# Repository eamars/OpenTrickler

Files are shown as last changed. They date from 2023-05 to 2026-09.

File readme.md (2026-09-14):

# Open Trickler - The Open Source Powder Trickler System

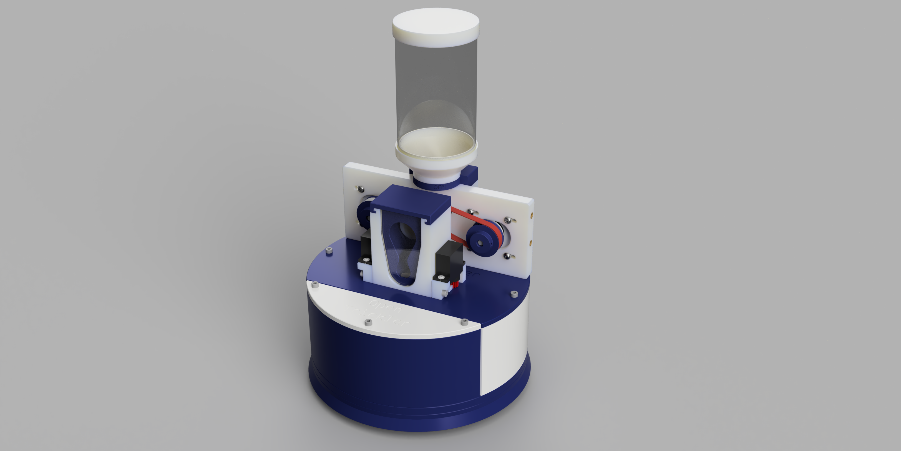
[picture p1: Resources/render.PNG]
render


Inspired by the [AutoTrickler v4](https://autotrickler.com/pages/autotrickler-v4) and [Super Trickler](https://supertrickler.com.au/), the OpenTrickler is designed be printed and assembled using common tools to build Voron printers.

Join our [discord server](https://discord.gg/ZhdThA2vrW) for help and development information. 

# Documentations

> [!TIP]
> You can follow the [Long Range Lab](https://www.youtube.com/@Longrangelab) build series to help understanding the build procedure.
> 
> * [Part 1 - Electronics](https://www.youtube.com/watch?v=DNZ34U0TyB8) 

* Bill of Material (BOM): [LINK](Manual/assembly.md#bom)
* Sourcing Guide: [LINK](Manual/sourcing_guide.md)
* Assembly Manual: [LINK](Manual/assembly.md)
* Initialization Guide: [LINK](Manual/initialization_guide.md)
* Powder Profile Tuning Guide: [LINK](Manual/tuning_guide.md)

Other supporting documents:

* Guide to order PCB from JLCPCB: [LINK](https://github.com/eamars/RaspberryPi-Pico-Motor-Expansion-Board/blob/main/production/README.md)
* A&D Scale Configuration Guide: [LINK](https://github.com/eamars/OpenTrickler-RP2040-Controller/blob/main/manuals/OpenTrickler%20manual%20for%20ADFX%20scale.pdf)
* G&G Scale Configuration Guide: [LINK](https://github.com/eamars/OpenTrickler-RP2040-Controller/blob/main/manuals/configure_g%26g_scales.md)
* OpenTrickler - Connect to Wireless: [LINK](https://github.com/eamars/OpenTrickler-RP2040-Controller/blob/main/manuals/connect_to_wireless.md)
* OpenTrickler - Update Firmware via USB: [LINK](https://github.com/eamars/OpenTrickler-RP2040-Controller/blob/main/manuals/firmware_update_via_usb.md)
* OpenTrickler - Build Companion (community-built interactive wizard for configuring, sourcing, printing, and tracking your build): [LINK](https://physikal.github.io/opentrickassist/)

# Print Guide

The printer need to be tuned at least for extruder e-stepts and flow as it has plastic to metal contact which requires certain tolerances. The Open Trickler can be printed in various materials.

* Main Material: ABS/PETG/PLA you name it.
* Belt: TPU 95A.
* 0.2mm layer height.
* 4x walls
* 5x tops and bottoms layers.
* 0.4~0.45mm line width
* 40% infill.

You should print provided STL with default orientation. **NO SUPPORT IS NEEDED FOR ALL PRINTED PARTS**.

# Controller

The Open Trickler Controller is split into following projects: 

* Custom PCB with Raspberry Pi Pico [Raspberry Pi Pico Motor Expansion Board](https://github.com/eamars/RaspberryPi-Pico-Motor-Expansion-Board)
* Firmware that utilises the Raspberry Pi RP2040 micro controller [OpenTrickler RP2040 Controller](https://github.com/eamars/OpenTrickler-RP2040-Controller)

# Interface Pattern

If you're a developer and would like to port the OpenTrickler to other platform/scale, you could use the mounting pattern as specified below. The interface is guaranteed to be consistent between minor revisions. 

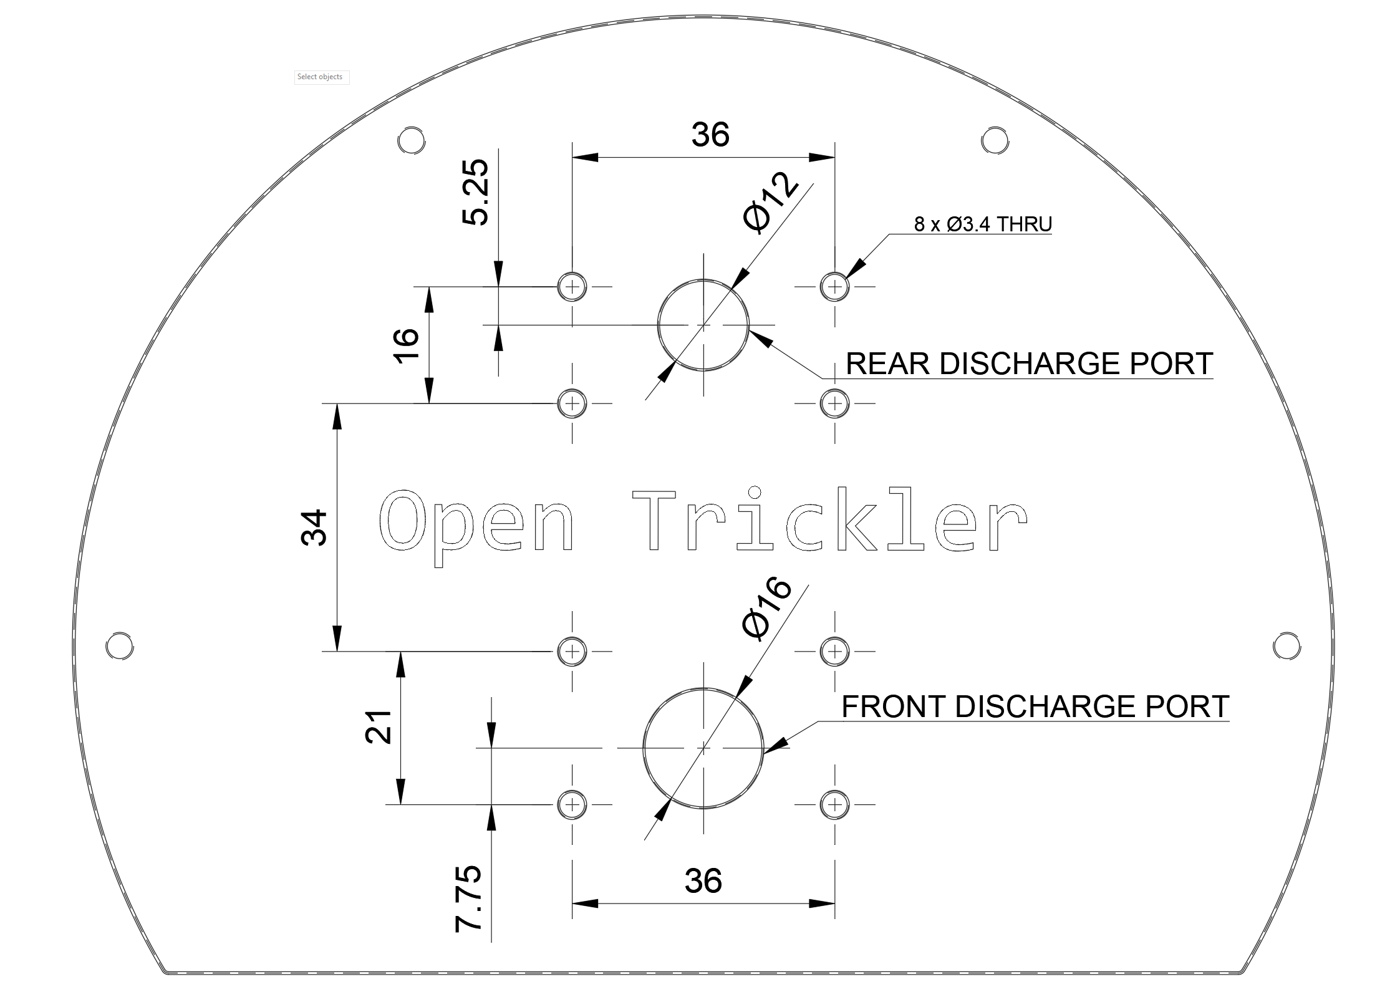
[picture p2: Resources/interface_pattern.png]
interface_pattern


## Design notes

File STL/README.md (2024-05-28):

# Print Guide

Depending on the selection of the scale, you need to print the STL file according to the table below. 

| Part\Scale | A&D fx120/300i | G&G JJ100B | G&G JJ223BF |
| --- |:---:|:---:|:---:|
| [A&D FX Shield](A&D%20FX%20Shield) | ✔️ | ❌ | ✔️ (partial, see [README](G&G%20JJ223BF%20Shield/README.md)) |
| [G&G JJ100B housing](G&G%20JJ100B%20housing) | ❌ | ✔️ | ❌ |
| [G&G JJ223BF Shield](G&G%20JJ223BF%20Shield) | ❌ | ❌ | ✔️ |
| [OpenTrickler](OpenTrickler) | ✔️ | ✔️ | ✔️ |
| [Powder Hopper](Powder%20Hopper) | ✔️ | ✔️ | ✔️ |

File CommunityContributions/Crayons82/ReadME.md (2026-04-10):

# **A&D FX Shield by Crayons82**

## Printing
- Layer hight .16
- Line width .42
- Top and bottom layer 4/5
- Wall layers 4/5
- Infill 25%

## I recommend printing from the Step files over the STL. Step files are more accurate and give better finish.

## BOM
- Heatset Inserts M3x5x4: 28

- M3x6 BHCS: 4

- M3x10 BHCS: 16

- M3x10 SHCS: 4 

- M3x12 SHCS: 4 

- WS2812B led Module 
 https://www.aliexpress.us/item/3256804431200048.html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

- 60 degree lens
https://www.aliexpress.us/item/3256810066508191.html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

## Assembly guide

 To assembly please reffer to Memphis's V1 readme.  
 
## additonal information 

Use the links above for the proper LEDs and lens. Lens may need a small amount of sanding on the edges to get them to fit propperly. Pay close attention for proper orientation of the lens as the back is rectanglular and shoud me orientated vertically 

In the images folder you will find 2 photos.  one images shows the front body with the led and wire between the front body and led wire housing. Make sure you insert the wire before sliding the front body into place and secureing.  The second image you can see the wire securment fasteners and the led retainer clip. 

Fine trickler inserts.  these inserts will screw into the large fine trickler tube. i recomment you screw each insert in before installing the tube to test fitment. should be tight and might need to screw in and out to get them to seat all the way. 

IF you have questions you can find me on the discord just send me a message and i'll respond as soon as i can.

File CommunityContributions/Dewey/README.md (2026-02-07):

# OpenTricklerDeweyMods


My personal mods for OpenTrickler!

I have made both Version 1 and 2 of the OpenTrickler, and it's my all-time favorite 3DP project. I've included a Version 2 cutout of the bearing plate on this homepage to test your bearing fit before printing full pieces, as I believe the bearing test should be your very first print. You can quickly adjust your X-Y Hole Compensation if needed before committing a large amount of your filament to the main pieces. EAMARS designed some bearing tolerance, so I recommend starting with zero Hole Compensation and go from there.

I've included some of my personal mods and my mods of other contributors. Have a look around and see if anything jumps out.

Mod highlights:
- Update 2/7/2026 - added Cup Holster for the Powder Cup in the A&D Shield Section
- Bearing Body for test fitting
- Hide the wires under the shield plate
- New rear bearing plate works with Ball Powder, both in version 1 and 2 of the Open Trickler
- Windowed front body using plexiglass, easily scored and cracked
- Front body with or without servos
- Front/Back spacer plates for tighter fit
- Wider top covers, easier to slide on
- Plug for the Lee Hopper adapter
- Small mods to Hayamini's controller board housing
- More to come....

I also have some free designs if you're interested in additional 3DP reloading/precision tools on Printables: https://www.printables.com/@DIY_Dewey

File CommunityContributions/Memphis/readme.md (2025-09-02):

# A&D FX Shield by Memphis

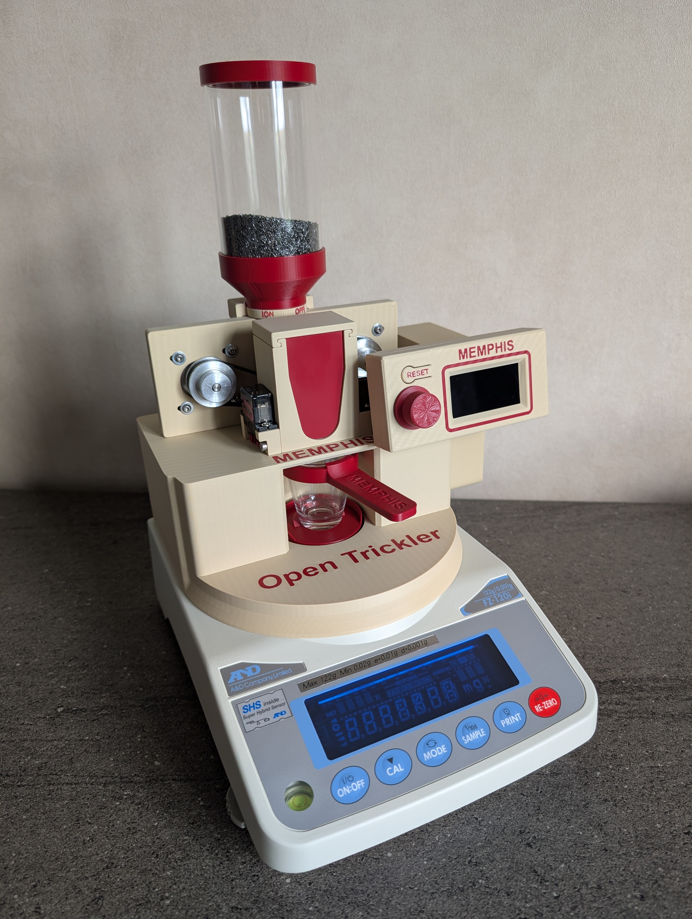
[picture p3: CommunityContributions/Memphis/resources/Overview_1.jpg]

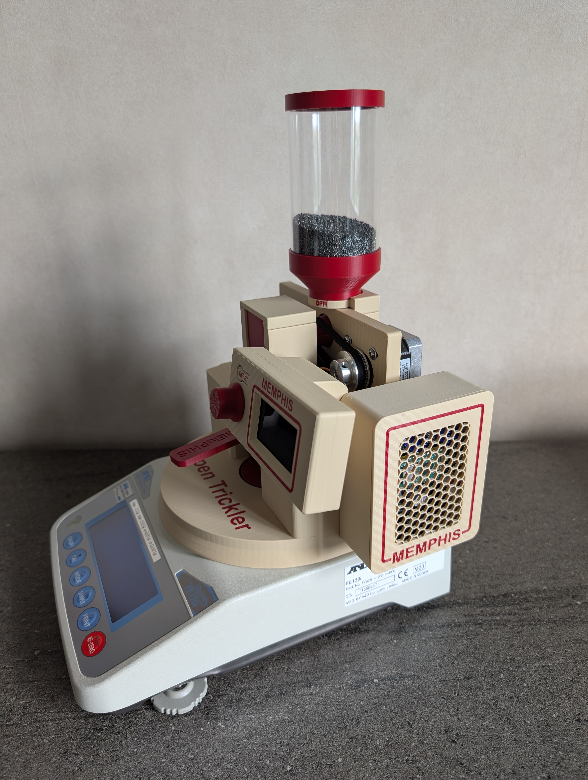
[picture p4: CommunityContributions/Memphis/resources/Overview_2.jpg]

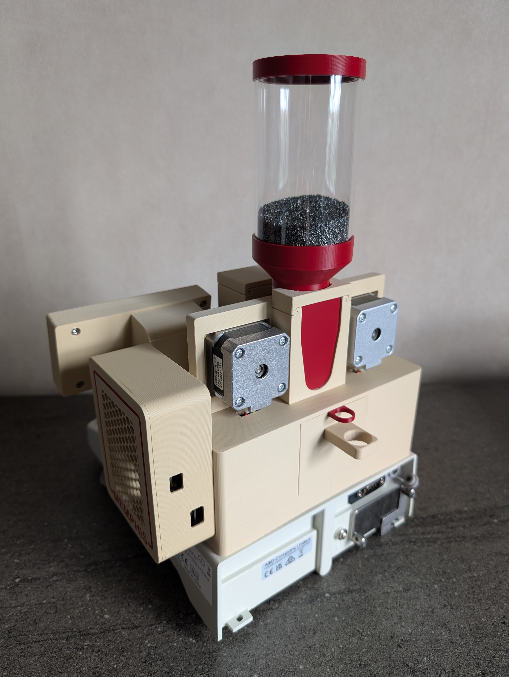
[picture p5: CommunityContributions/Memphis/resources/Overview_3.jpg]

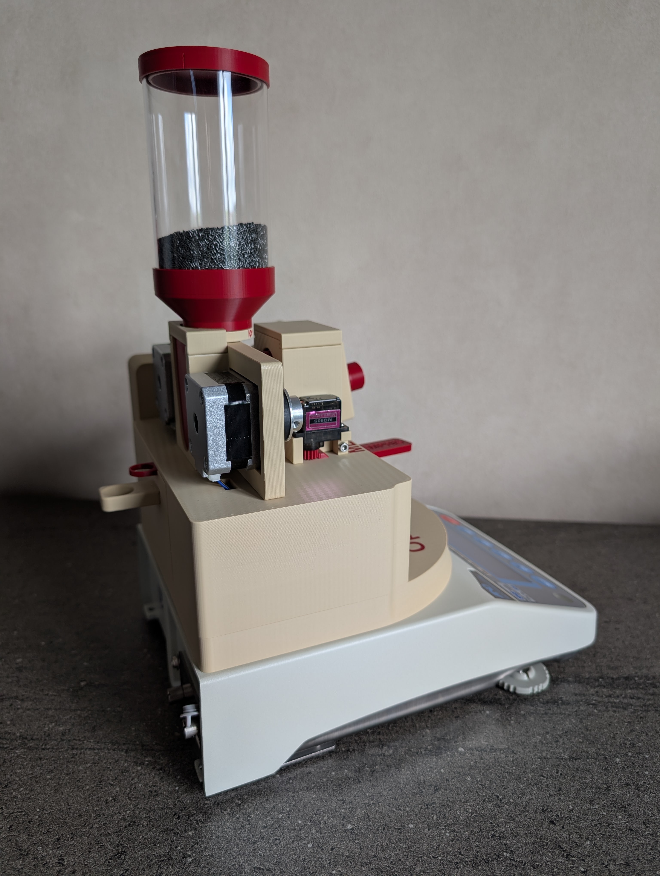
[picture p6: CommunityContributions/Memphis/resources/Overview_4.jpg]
  

## BOM

- Heatset Inserts M3x5x4: 24
- Nut M3: 4
- M3x6 BHCS: 4
- M3x10 BHCS: 16
- M3x10 SHCS: 4 
- M3x12 SHCS: 4  

- A shot glass, height: 50mm, diameter at top: 41.6mm
- An o-ring 35mm in diameter  

- WS2812B led with cable and connector
- 13mm lens

## Assembly guide

### Rear discharge mount
Use 4x M3x12 SHCS with [rear_discharge_mount.stl](STL/rear_discharge_mount.stl) to join the [rear_body_without_holes.stl](STL/rear_body_without_holes.stl) to the [scale_shield.stl](STL/scale_shield.stl).
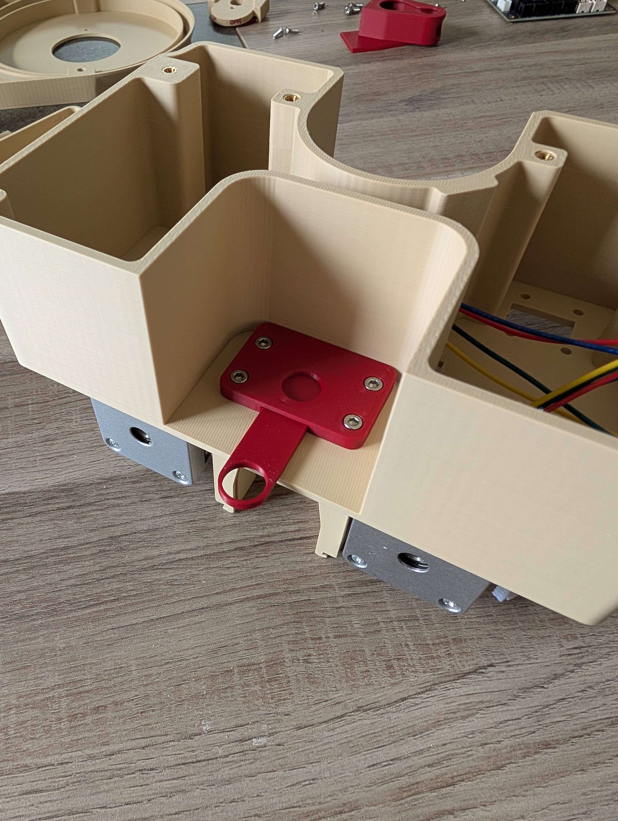
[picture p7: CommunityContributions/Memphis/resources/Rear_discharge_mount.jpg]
  

### LED
Use one of the connectors provided with the 3D mellow PCB.  
Be sure to use the LED's DI pin.  
You need a 13mm diameter lens.  
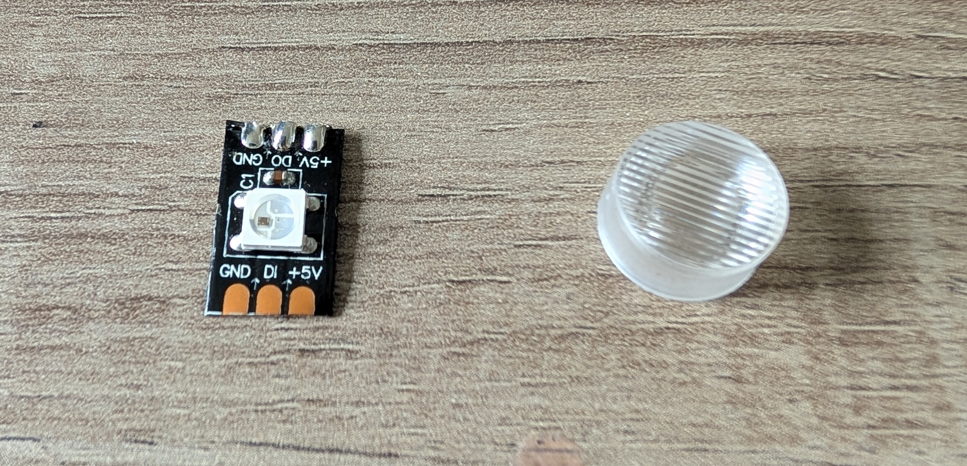
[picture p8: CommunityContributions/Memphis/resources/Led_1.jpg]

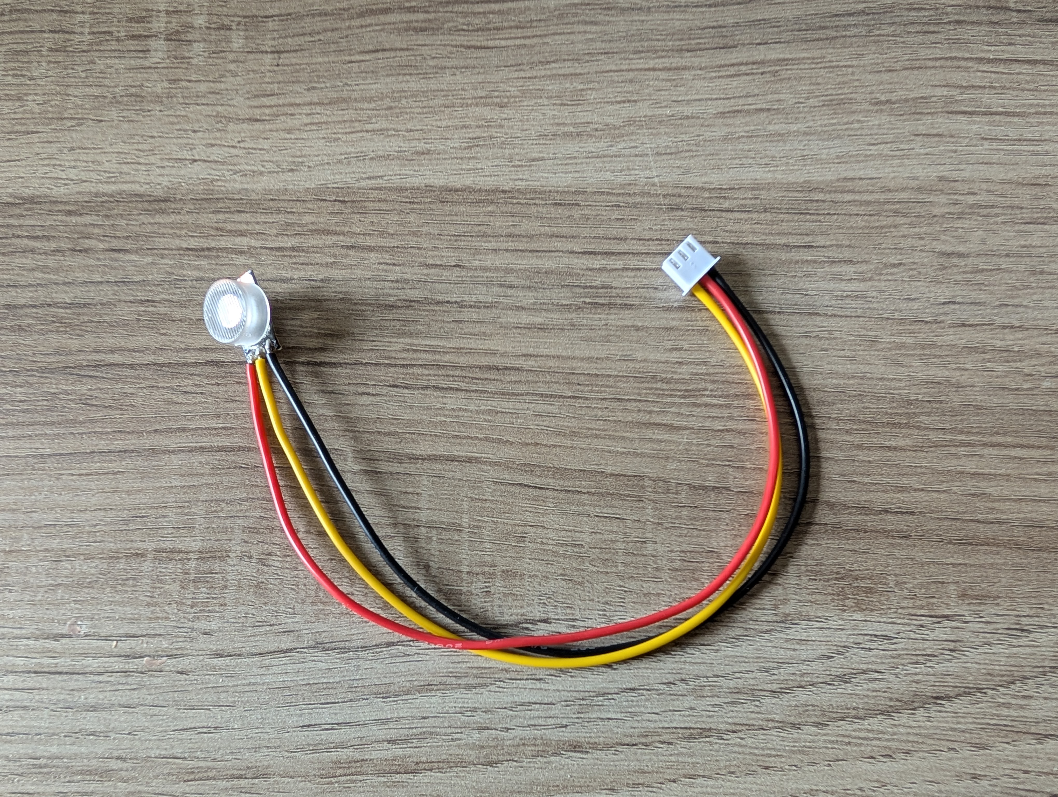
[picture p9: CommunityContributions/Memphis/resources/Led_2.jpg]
  

Place the lens in the hole after adjusting it if necessary with a file and sandpaper.
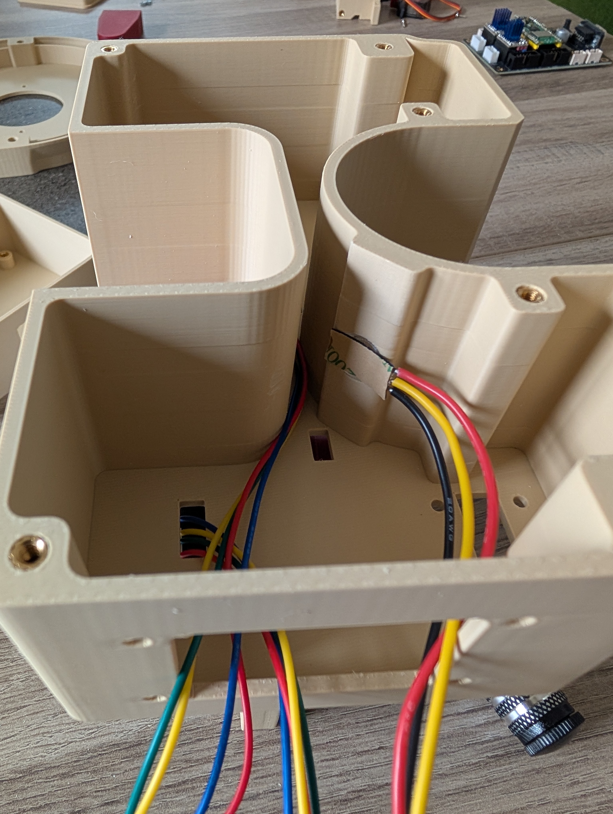
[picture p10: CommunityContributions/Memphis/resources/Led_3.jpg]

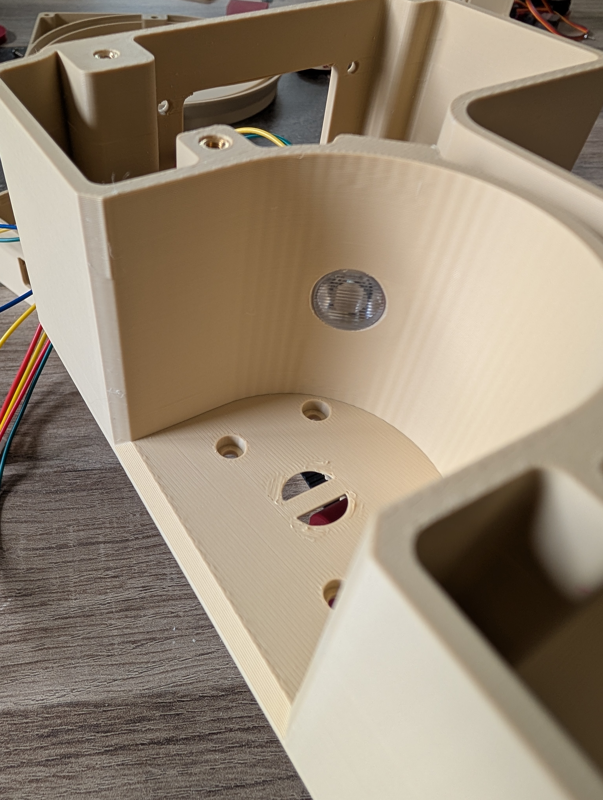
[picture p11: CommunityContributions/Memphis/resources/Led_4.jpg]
  

### Display
Melt 8x heatset into the [display_assy_bracket.stl](STL/display_assy_bracket.stl).  
Use 4x M3x10 BHCS to join the [display_assy_body.stl](STL/display_assy_body.stl) to the [display_assy_bracket.stl](STL/display_assy_bracket.stl).
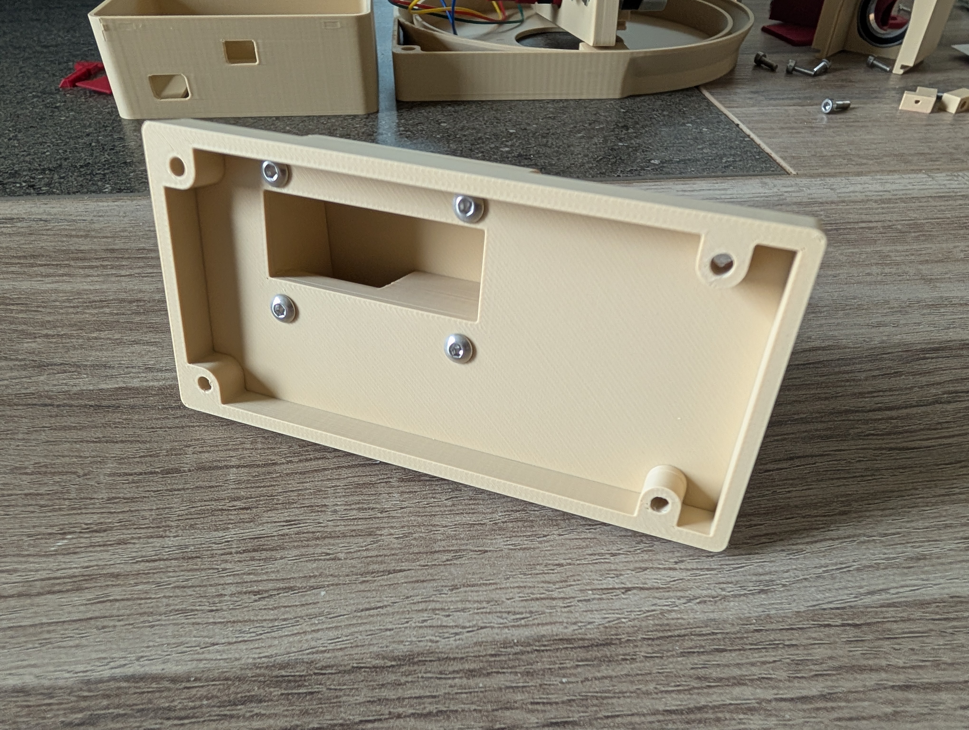
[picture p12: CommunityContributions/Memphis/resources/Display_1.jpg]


Route the connection cables as shown in the photo.


Melt 4x heatset into [the display_assy_front.stl](STL/display_assy_front.stl).  
Use 4x M3x12 SHCS to join [display_assy_body.stl](STL/display_assy_body.stl) to the [the display_assy_front.stl](STL/display_assy_front.stl).
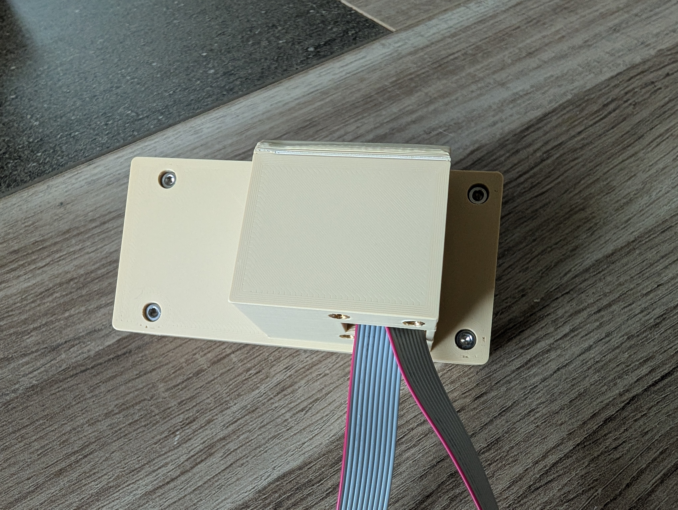
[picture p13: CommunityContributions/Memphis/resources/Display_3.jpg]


Use 4x M3x10 BHCS to join the [display_assy_bracket.stl](STL/display_assy_bracket.stl) to the [scale_shield.stl](STL/scale_shield.stl).
  

### Enclosure
Melt 4x heatset into the [enclosure_bottom.stl](STL/enclosure_bottom.stl) to be able to fix the PCB.  
Use 4x M3x10 BHCS and 4x M3 nuts to join [enclosure_bottom.stl](STL/enclosure_bottom.stl) to [scale_shield.stl](STL/scale_shield.stl).  
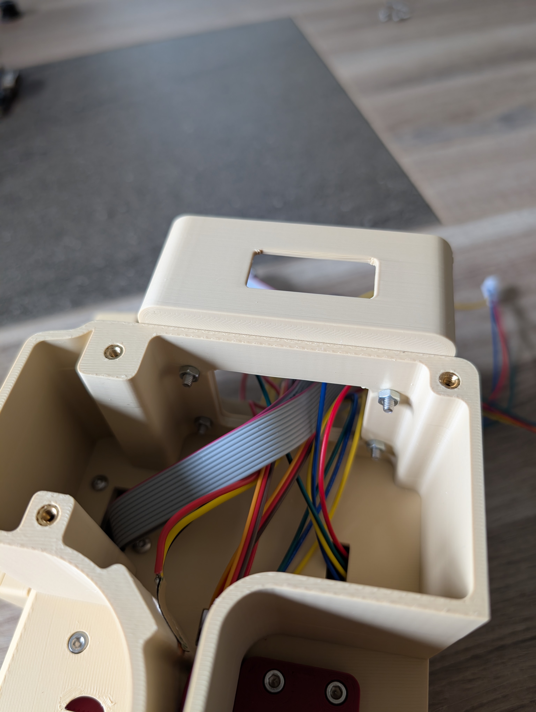
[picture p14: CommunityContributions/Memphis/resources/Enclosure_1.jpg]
  

After passing all the cables, fix the PCB with 4x M3x6 BHCS screws.
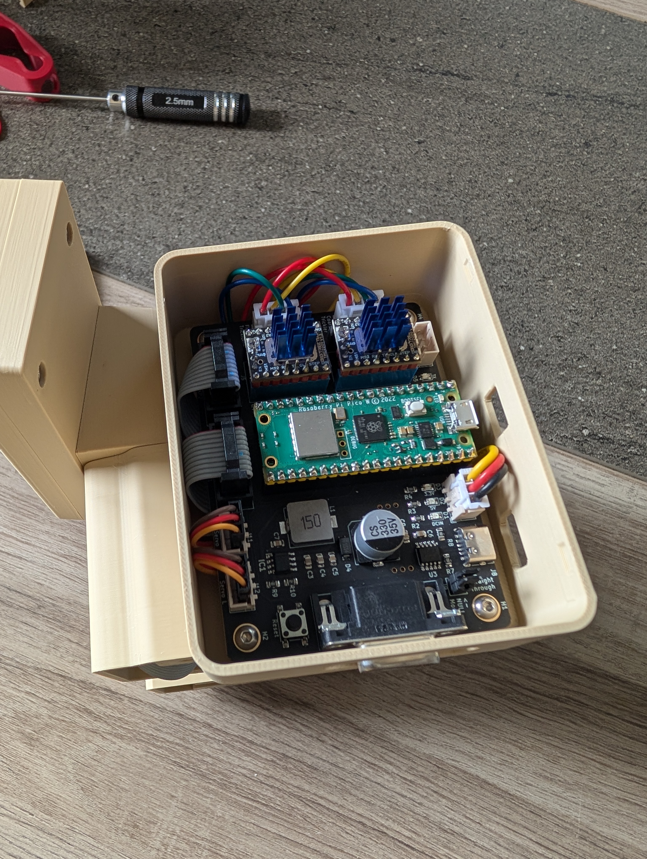
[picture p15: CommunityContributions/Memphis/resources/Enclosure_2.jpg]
  

The case cover ([enclosure_top.stl](STL/enclosure_top.stl)) is simply snapped on.

### Scale base
Overview with all cables:
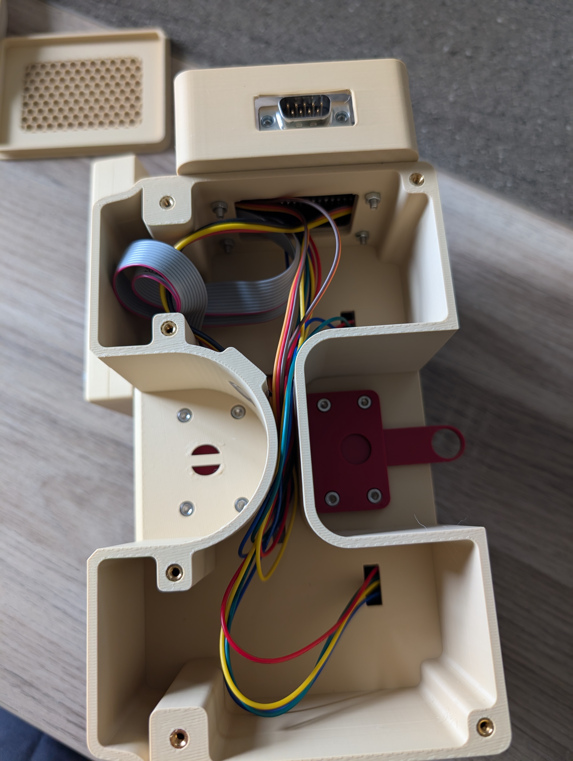
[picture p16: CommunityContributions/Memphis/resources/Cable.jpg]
    
Use 4x M3x10 SHCS and 2x M3x10 BHCS to join the [scale_base.stl](STL/scale_base.stl) to the [scale_shield.stl](STL/scale_shield.stl).
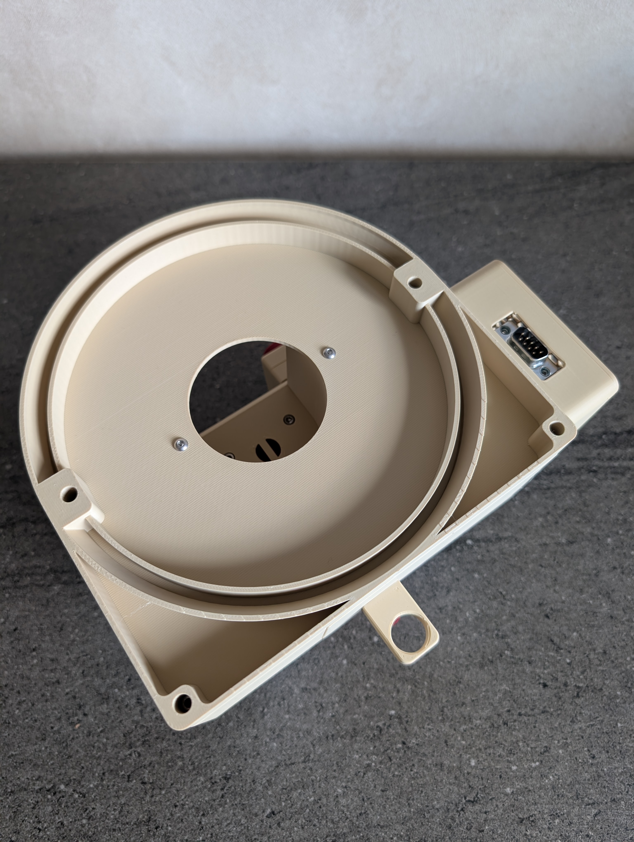
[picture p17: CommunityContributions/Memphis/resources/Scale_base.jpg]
  

## Cup base 
Use the first weighing plate and add a piece of tape to fix the [cup_base.stl](STL/cup_base.stl).
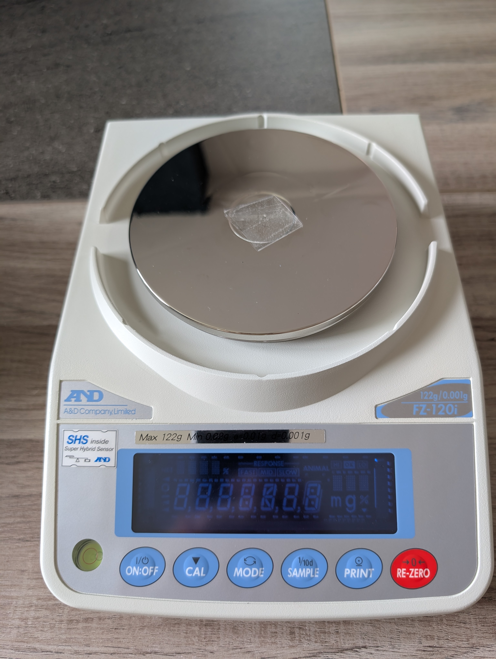
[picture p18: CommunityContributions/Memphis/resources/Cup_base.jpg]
  

## Rear discharger cup
[rear_discharger_cup.stl](STL/rear_discharger_cup.stl)  
[rear_discharge_cup_ring.stl](STL/rear_discharge_cup_ring.stl)  
2x heatset  
2x M3x10 SHCS
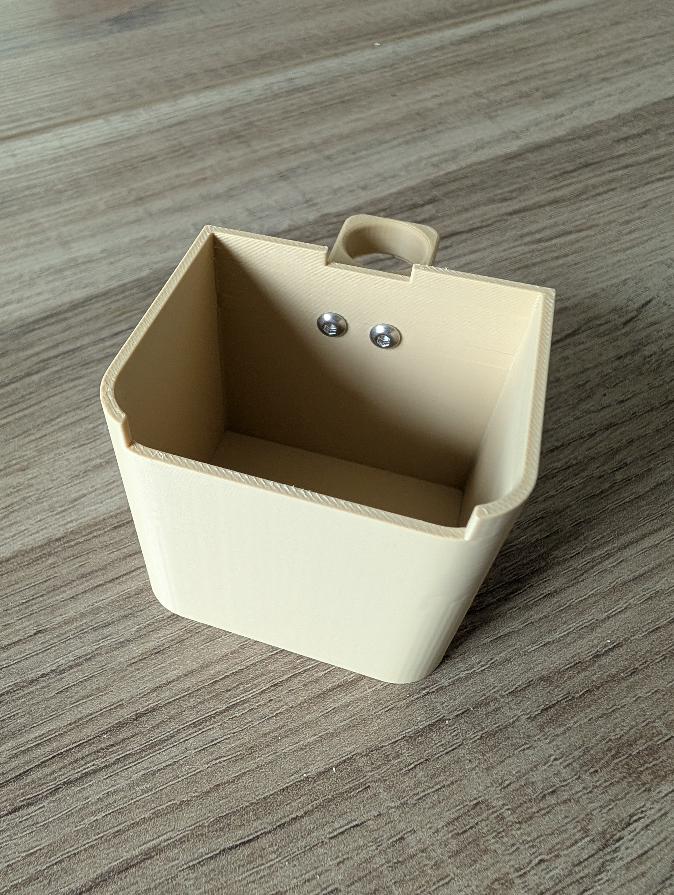
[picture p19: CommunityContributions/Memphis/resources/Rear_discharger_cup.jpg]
  

## Powder cup
It is possible not to use the o-ring if your print is very tight.  
[powder_cup_handle.stl](STL/powder_cup_handle.stl)
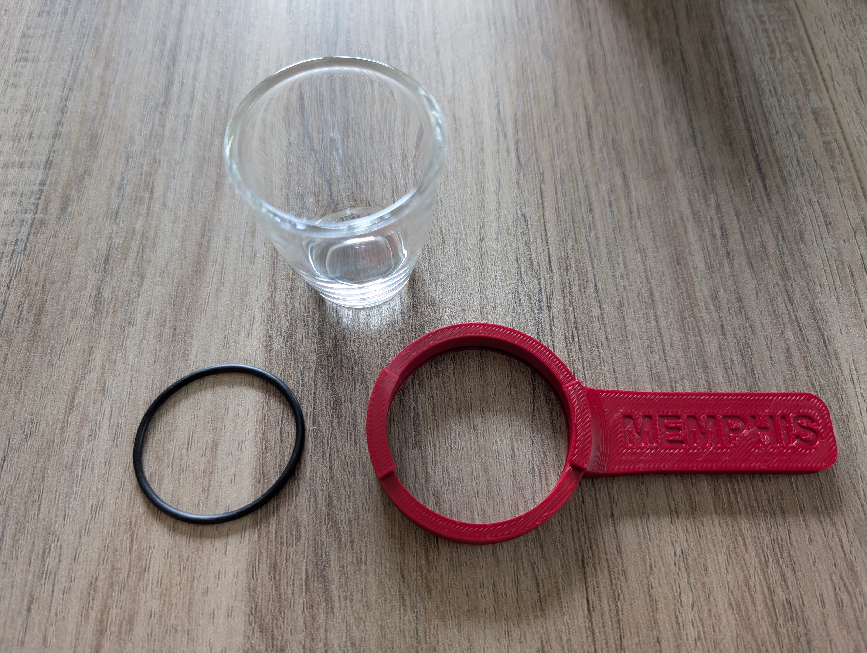
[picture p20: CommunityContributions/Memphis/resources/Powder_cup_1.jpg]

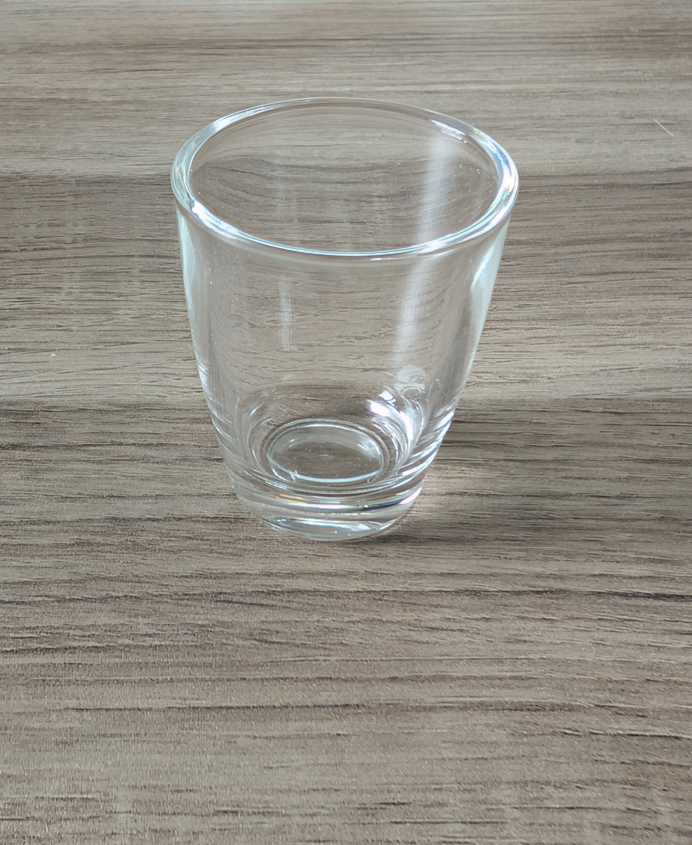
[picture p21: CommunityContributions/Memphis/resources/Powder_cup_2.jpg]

  

## Options:
### Powder hopper:
Clear acrylic tube, outer diameter: 60mm and inner diameter: 56mm  
[hopper_base_plexi.stl](STL/hopper_base_plexi.stl)  
[hopper_cap.stl](STL/hopper_cap.stl)
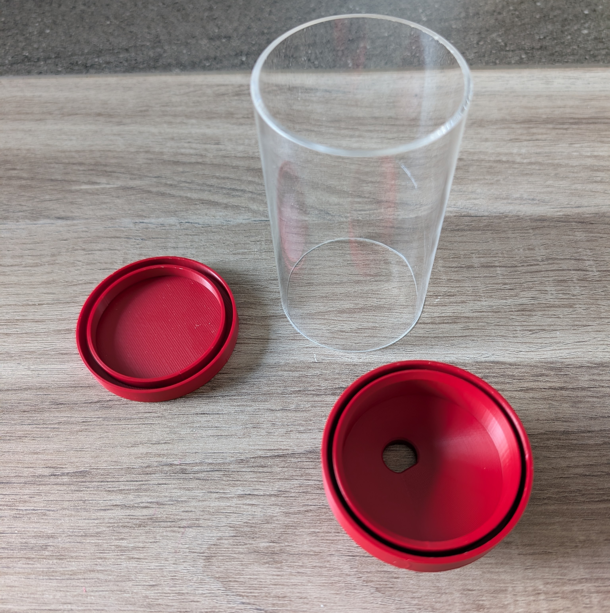
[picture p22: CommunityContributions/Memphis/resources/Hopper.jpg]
  

### Rear body:
Rear body without holes on the sides ([rear_body_without_holes.stl](STL/rear_body_without_holes.stl))
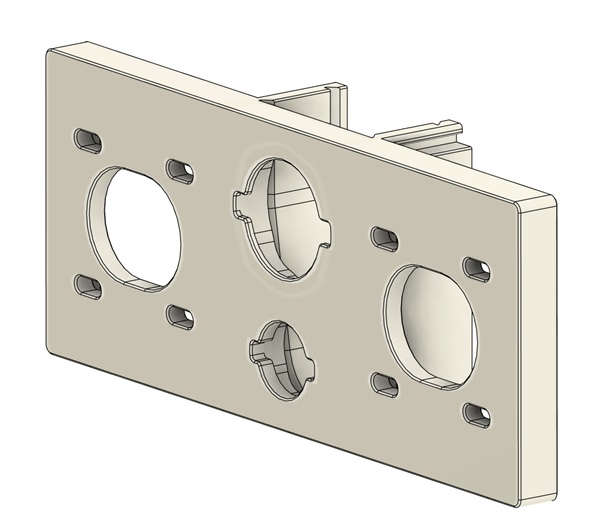
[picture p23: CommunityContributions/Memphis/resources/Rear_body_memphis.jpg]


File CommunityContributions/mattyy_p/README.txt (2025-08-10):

Small Trickler Tube Mod
1) Print inner portion in vase mode - use a brim if necessary
2) Print outer portion per normal printing parameters
3) Apply adhesive to exterior of the vase mode print and slide into place

Extended Servo Support Mod
1) Print per normal printing parameters
2) You must print LEFT and RIGHT sides individually - they are not interchangeable

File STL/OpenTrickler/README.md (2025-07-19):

# OpenTrickler Print and Assembly Guide

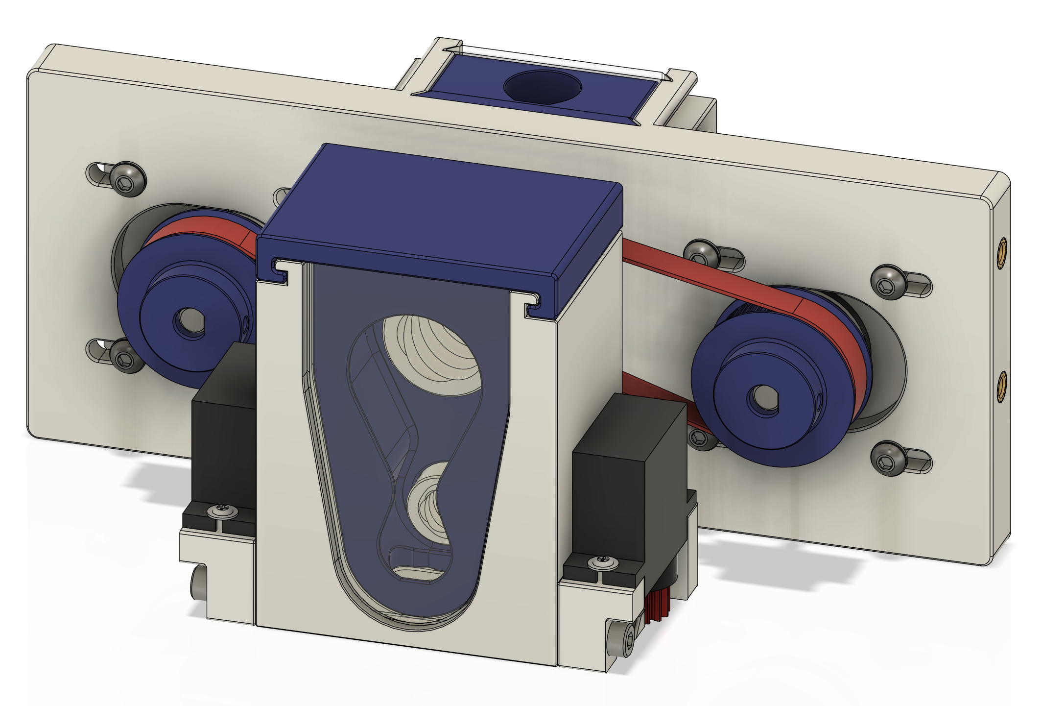
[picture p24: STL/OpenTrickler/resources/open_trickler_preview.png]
opentrickler_preview


## Print Guide

### Main Body

| Filename | Quantity | Alternative | Remarks |
| --- | --- | --- | --- |
| [40_teeth_gt2_pulley_x2.stl](40_teeth_gt2_pulley_x2.stl) | 2 | | Can be substituted with aftermarket metal 40T pulley. |
| [front_body.stl](front_body.stl) | 1 | | The front body of the OpenTrickler. |
| [front_body_cover.stl](front_body_cover.stl) | 1 | | The top cover that sits on top of the front body. |
| [front_rear_door_x2.stl](front_rear_door_x2.stl) | 2 | | Recommended to print in translucent material. |
| [GT2_82T_Belt.stl](GT2_82T_Belt.stl) | 1 | | (Optional Printable Part) Can be substituted with aftermarket 83T (166 mm) GT2 belt. This part has to be printed in TPU or any flexible material. |
| [GT2_86T_Belt.stl](GT2_86T_Belt.stl) | 1 | | (Optional Printable Part) Can be substituted with aftermarket 87T (174 mm) GT2 belt. This part has to be printed in TPU or any flexible material. |
| [large_rotary_tube.stl](large_rotary_tube.stl) | 1 | | Recommended to print with random Z seam position. |
| [rear_body.stl](rear_body.stl) | 1 | | The rear body of the OpenTrickler |
| [small_rotary_tube_low_flow.stl](small_rotary_tube_low_flow.stl) | 1 | [small_rotary_tube_mid_flow.stl](small_rotary_tube_mid_flow.stl) or [small_rotary_tube_high_flow.stl](small_rotary_tube_high_flow.stl) | Recommended to print with random Z seam position.<br/> - The default design has blocked rear end, good for normal and generic flow application. <br/> - The alternative design has flow through rear end, good for high flow application, e.g,. magnum charges. |

### Servo Gate

| Filename | Quantity | Alternative | Remarks |
| --- | --- | --- | --- |
| [ServoGate/left_servo_hanger.stl](ServoGate/left_servo_hanger.stl) | 1 | | Left servo hanger (from the front perspective) |
| [ServoGate/left_shutter.stl](ServoGate/left_shutter.stl) | 1 | | Left shutter underneath the front body (from the front perspective) |
| [ServoGate/right_servo_hanger.stl](ServoGate/right_servo_hanger.stl) | 1 | | Right servo hanger (from the front perspective) |
| [ServoGate/right_shutter.stl](ServoGate/right_shutter.stl) | 1 | | Right shutter underneath the front body (from the front perspective) |
| [ServoGate/spur_gear_x2.stl](ServoGate/spur_gear_x2.stl) | 2 | | Spur gear for both servo motors. Can be opted out if you're not planning to use servo gate |

### Volume Reducer

| Filename | Quantity | Alternative | Remarks |
| --- | --- | --- | --- |
| [VolumeReducer/FrontVolumeReductionInsert_Bottom.stl](VolumeReducer/FrontVolumeReductionInsert_Bottom.stl) | 1 | | Front volume reducer body |
| [VolumeReducer/FrontVolumeReductionInsert_Top.stl](VolumeReducer/FrontVolumeReductionInsert_Top.stl) | 1 | | Serving as front bearing plate |
| [VolumeReducer/RearVolumeReductionInsert_Bottom.stl](VolumeReducer/RearVolumeReductionInsert_Bottom.stl) | 1 | | Rear volume reducer body |
| [VolumeReducer/RearVolumeReductionInsert_Top.stl](VolumeReducer/RearVolumeReductionInsert_Top.stl) | 1 | | Serving as rear bearing plate  |

## BOM

| **Name** | **Quantity** | **Remarks** |
| --- |:--- |:--- |
| M2x8 self-tapping | 4 | Each servo motor should come with 2x screw in the package |
| Heatset Inserts M3x5x4 | 18 | |
| M2.5x3.5 BHCS | 2 | Each servo motor should come with 1x screw in the package |
| M3x8 BHCS | 8 | |
| M3x12 SHCS | 2 | |
| Shim Washer | 8 | OD=6mm, ID=3mm, Thick=0.5mm |
| 6804 Bearing | 2 | |
| 6801 Bearing | 2 | |
| Nema 17 Stepper Motor  | 2 | See the sourcing guide for recommendations |
| TowerPro MG90s | 2 | 180 deg servo motor is recommended. Other servo motors that have identical footprint than MG90s, for example, SG90, S0009M can also be used. |

## Tools

* 2.5 mm hex driver

* 2.0 mm hex driver

* Small phillips screwdriver

## Assembly of Rear Body

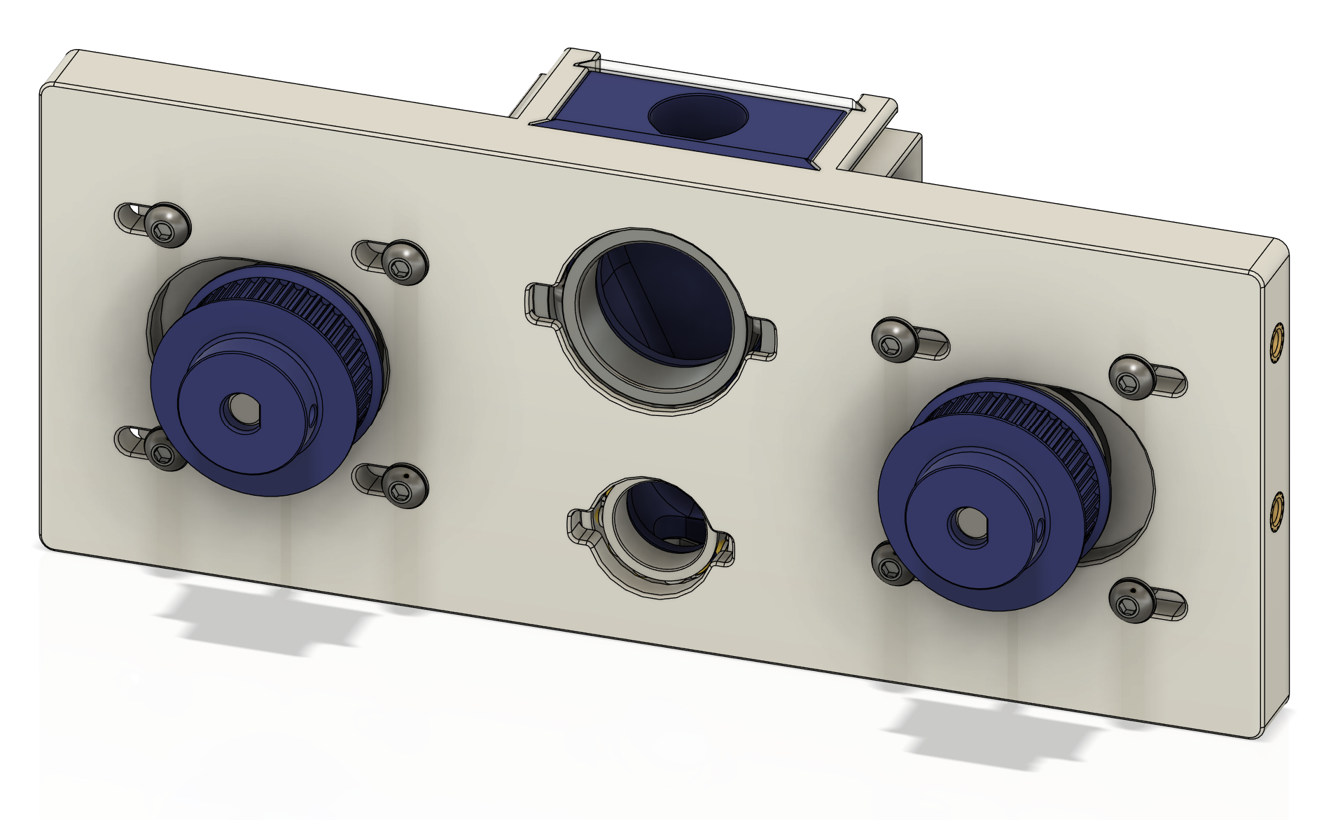
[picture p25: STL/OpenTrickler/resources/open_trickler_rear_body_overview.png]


### Component Prep

Melt 4x heatset inserts to the bottom of the [rear_body.stl](rear_body.stl). Make sure the heatset inserts are sitting flush with the surface.

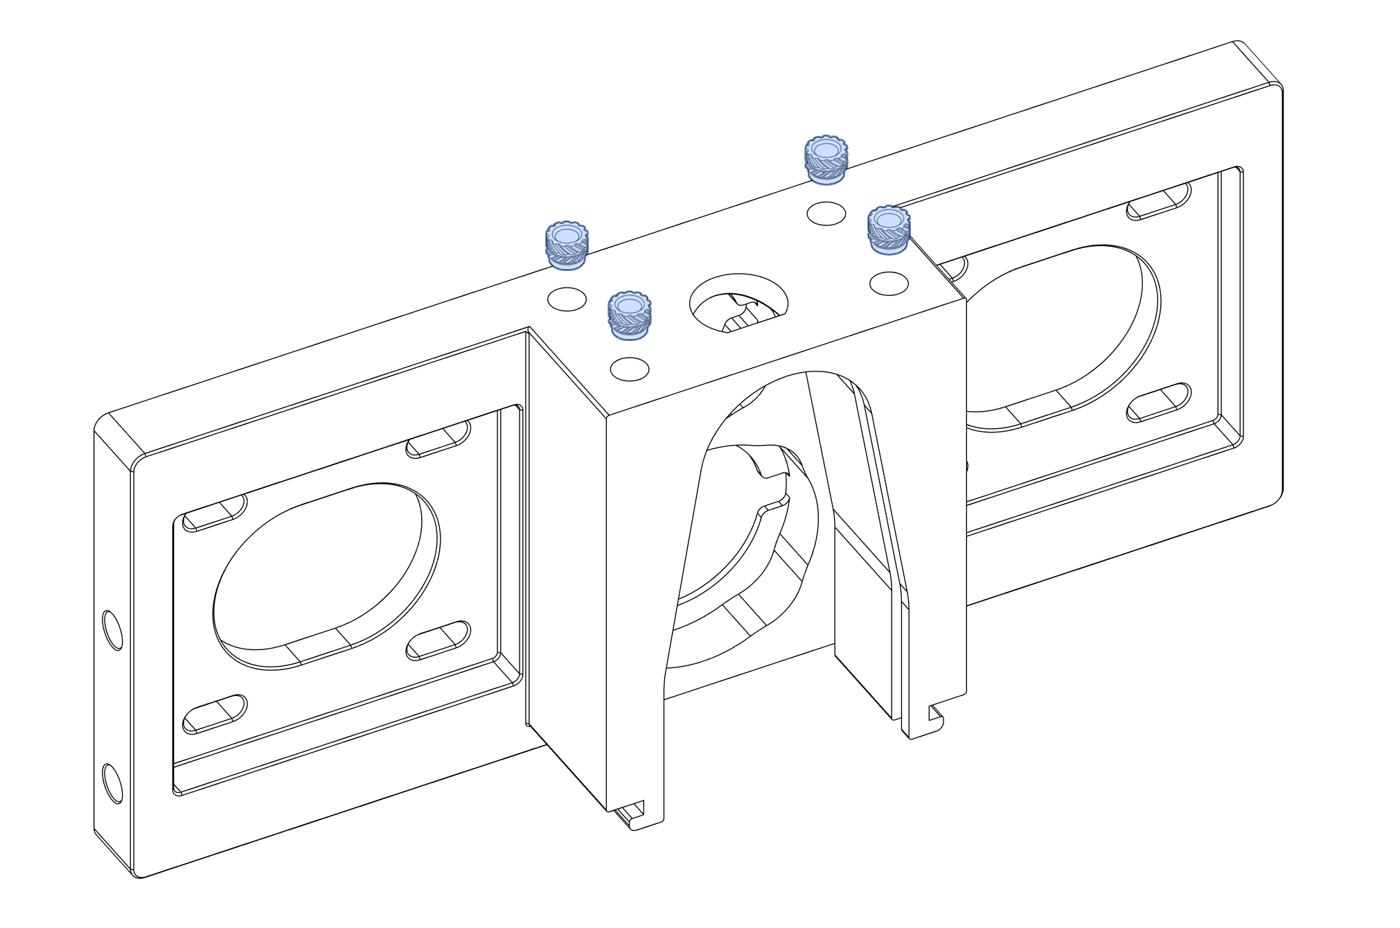
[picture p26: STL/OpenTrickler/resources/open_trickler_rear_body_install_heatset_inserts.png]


Optionally, the additional 4x heatset inserts can be melt to either sides of the body to support the installation of additional parts, for example, the [WeightHolder](Optional/WeightHolder). 



### Assembly

Press 6804 bearing to the top pocket and 6801 bearing to the bottom pocket of [rear_body.stl](rear_body.stl). [Printable bearing insert helpers](Tools) are supplied to use with benchtop vise if the bearings can't be pressed in by hands. 



Slide the [RearVolumeReductionInsert_Top.stl](VolumeReducer/RearVolumeReductionInsert_Top.stl) to the first cut out next to the bearings from the top, serving as the bearing cover. Ensure the part is sitting flush with the top surface. 



Push the [RearVolumeReductionInsert_Bottom.stl](VolumeReducer/RearVolumeReductionInsert_Bottom.stl) from the rear opening against the bearing cover. 



Then slide the [front_rear_door_x2.stl](front_rear_door_x2.stl) to the second cut out from the top, Ensure the part is sitting flush with the top surface.



Use 8x M3x8 BHCS screws with the optional M3 shim washers to mount two stepper motors onto the [rear_body.stl](rear_body.stl), but don't tighten them yet. Make sure the motor can slide left to right with little to none resistance.



Slide 2x [40_teeth_gt2_pulley_x2.stl](40_teeth_gt2_pulley_x2.stl) to the motor shaft but don't tighten the set screws yet. The pulley position will be adjusted in the later step.



The rear body assembly is now complete. 

## Assembly of Front Body



### Crimping

The [Pico Motor Expansion Board v2](https://github.com/eamars/RaspberryPi-Pico-Motor-Expansion-Board) assumes the servo motor comes with the JST PH2.54 connector. You may need to re-crimp the connector to 3pin JST PH 2.54 connectors in order to connect the servo motor to the motor expansion board. The colour code for MG90s servo motor is provided below.

wiring_colour_code

### Component Prep

Melt 4x heatset inserts to the bottom of the [front_body.stl](front_body.stl) and 2x to either sides. Make sure the heatset inserts are sitting flush with the surface.



### Assembly

Use 2x M3x12 SHCS to fix the [left_servo_hanger.stl](ServoGate/left_servo_hanger.stl) and [right_servo_hanger.stl](ServoGate/right_servo_hanger.stl) to both sides. Servo hangers are polarised. A dot on the body is used to indicate the face pointing towards the servo motor.

install_servo_hangers

Slide the [spur_gear_x2.stl](ServoGate/spur_gear_x2.stl) to the output gear of both servo motors. Make sure the side with the teeth is pushed against the gear. Use the M2.5x3.5 BHCS (came with the servo motor) to fix the spur gear in place.

install_spur_gear

Use 4x M2x8 self-tapping screw to fix the servo motors to the front body at both sides. Make sure the servo motors are installed so the spur gear is closer to the rear of the body.

install_servo_motors

Press 6804 bearing to the top bearing pocket and 608 to the bottom bearing pocket. [Printable bearing insert helpers](Tools) are supplied to use with benchtop vise if the bearings can't be pressed in by hands.



Slide the [FrontVolumeReductionInsert_Top.stl](VolumeReducer/FrontVolumeReductionInsert_Top.stl) to the first cut out next to the bearing from the top, serving as the bearing cover. Ensure the part is sitting flush with the top surface. 



Push the [FrontVolumeReductionInsert_Bottom.stl](VolumeReducer/FrontVolumeReductionInsert_Bottom.stl) from the front opening against the bearing cover. 



Slide the [front_rear_door_x2.stl](front_rear_door_x2.stl) to the cut out, the front door should sit flush with the top of the [front_body.stl](front_body.stl).

open_trickler_front_body_install_front_door

Slide the [front_body_cover.stl](front_body_cover.stl) to the groove top of the [front_body.stl](front_body.stl) then the front body assembly is complete.

open_trickler_front_body_install_front_body_cover

### Servo Gate Tuning Guide

#### Connect Servo Motors to the Controller Board

* For Pico Motor Expansion Board v1 + PWM Expansion Board, you need to connect the left servo motor (from the front perspective) to J1, and the right servo motor to J2.

* For Pico Motor Expansion Board v2, you need to connect the left servo motor (from the front perspective) to J6, and the right servo motor to J7.

#### Servo Motor Control Basics

The TowerPro MG90s uses PWM duty cycle to accept external command for position control. The period of the "on" cycle determines the absolute position shown in the table below. Intermediate positions between -90 to 90 degrees are linearly interpolated with respect to the duration of the "on" period.

pwm_servo_control

The OpenTrickler uses the duty cycle (the ratio of the time between on and off per cycle) as the input to control the opening and closing of the servo gate.

| Period | Absolute Position | Duty Cycle (period/20ms) |
| --- | --- | --- |
| 1 ms | -90 degree | 0.050 |
| 1.5 ms | 0 degree | 0.075 |
| 2 ms | 90 degree | 0.100 |

The servo gate opening and closing duty cycle need to be tuned before the final assembly. Please follow the [initialization guide](https://github.com/eamars/OpenTrickler/blob/main/Manual/initialization_guide.md) to bring up the wireless controller. The following steps assumes the WebUI is functional. 

#### Enable Servo Gate

The servo gate is disabled by default. You need to navigate to the WebUI -> Settings -> Servo Gate, toggle the "Servo Gate Enable" option from No to Yes, then hit the Apply button with "Save to EEPROM" option. Then restart the OpenTrickler controller by pressing the reset button, or reset from the web interface. 

enable_servo_gate

#### Tune the Shutters

The left shutter is assigned to Shutter 0. By default the shutter is operating at a very limited range. You need to follow the below steps. 

1. Flip the front body up-side-down. 

2. Set the shutter 0 close duty cycle to 0.1, then apply the settings. 

3. Navigate to the Trickler page, click the Gate Close button. Wait for the servo motor to change position.

4. Place the left shutter to the bottom cut out at the closed position (demonstrated below). Make sure the left shutter engages with the spur gear. If not, adjust the shutter 0 close duty cycle up a bit (around 0.005) from the settings and click the Gate Close button again. 
   place_left_shutter

5. Click Gate Open Button, wait for the servo motor to change position. 

6. The shutter is now moved to the open position. If the shutter is not fully closed, you need to adjust the shutter 0 open duty cycle up, then click the Gate Open Button. This process may need to be repeated multiple times until the full open duty cycle is termined by experiment. 

7. Repeat above procedures with the shutter 1. Note the shutter 1 is operating at the opposite position, where the open and close duty cycle is roughly opposite to the shutter 0. 

8. **(Important)** make sure the settings are saved in the end, by "Save to EEPROM". 

Once the shutter open and close angles are tuned, you can continue with the full body assembly. 

## Assembly of Open Trickler Front and Rear Body

Note: this step requires the top assembly from one of the scale shield. The manual will use the top assembly from A&D FX Shield as an example. 

### Assembly

Mount the rear body assembly to the scale shield with fasterners. 

Insert both [large_rotary_tube.stl](large_rotary_tube.stl) and one of the small rotary tubes through the rear bearing. You may experience some resistance subject to the 
tolerance of the printed part. It is recommended to sand the mating surface of the tube if it cannot be inserted into the bearing by hand. 

- [small_rotary_tube_low_flow.stl](small_rotary_tube_low_flow.stl): for small size kernels, or ball powder. 

- [small_rotary_tube_mid_flow.stl](small_rotary_tube_mid_flow.stl): For medium size kernels. 

- [small_rotary_tube_high_flow.stl](small_rotary_tube_high_flow.stl): For large size kernels. 

*Note: Only one of the small rotary tube is required. If you are uncertain of which tube to use, you can always start with the low flow tube.*



Slide the pully assembly towards rotary tubes to the nearest position. Once done, slide the belt onto rotary tubes and pulleys. Make
sure the longer belt is connected to the motor on the right side. **Do not tension the belt, nor adjust the depth of the pulley for now.**



Slide the front body assembly over the rotary tubes through bearings. The front body assembly need to be pushed all the way to align with four mounting holes, then fix the front body assembly with the scale lid using fasterners. 

*Note: You may need to flip the full assembly up-side-down to ensure the servo gate doesn't accidently move or shift when sliding the front body over the bearings.*



Slide the [Powder Hopper](../Powder%20Hopper/) to the rear body, then the OpenTrickler is fully assembled. 



## Post Installation Adjustments

Assuming you have already built the suitable scale shield and attached the OpenTrickler to it, you can finalize the installation by tensioning the belt. 

### Adjust Pulley Depth

Look through the unit from the left and right side, push or pull the pulley on the shaft to align the flange with the rotary tubes.



### Tension The Belt

You need to adjust the tension of the belt. First loosen 4x M3x8 BHCS used to secure stepper motors. 
Then pull motors slightly to tension the belts. Once done, tighten all 4 screws. Repeat the process for both larger and small rotary tube motors.



# Congratulations

Your Open Trickler is now assembled!

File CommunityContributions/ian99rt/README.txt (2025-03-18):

Notes for Front Housing: 
1) Should be printable without supports 
2) Only works with Gearless Shutters
3) Uses a 2mm x 38mm x 63mm acrylic window for the front cover: cut from https://www.amazon.com/dp/B0CZHL7RZK?ref_=ppx_hzsearch_conn_dt_b_fed_asin_title_1&th=1
4) Uses included servo mounting screws

Notes for GearLess Shutter:
1) Uses Shoulderbolts with needle roller bearings as pin/slot connection instead of gears
2) Allows for very fast shutter motion and should be very wear resistant

Amazon Links:

Qty. 2x, 3mm Shoulder Bolts, M2.5, 16mm Long: https://www.amazon.com/dp/B0D31WBFV2?ref=ppx_yo2ov_dt_b_fed_asin_title
Qty. 2x, HF0306 Needle Roller Bearings 3mm x 6.5mm x 6mm: https://www.amazon.com/dp/B0DJ77X8SZ?ref=ppx_yo2ov_dt_b_fed_asin_title&th=1
Qty. 2X, M2.5 Hex Nuts: https://www.amazon.com/dp/B07H3WGLJN?ref=ppx_yo2ov_dt_b_fed_asin_title

Notes for 1 Piece Volume Fillers
1) Should be printable without supports
2) Front volume filler aims to control powder all the way to the shutter without horizontal ledges

Notes for 3mm thicker Front Discharge plate
1) Steeper angle to reduce powder hanging in chute (was having issues with hidden H4350 dropping when shutter closed)
2) Requires shorter Powder cup base to fit under the thicker plate

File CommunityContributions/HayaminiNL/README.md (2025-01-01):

# @HayaminiNL contribution

* OpenTrickler controllerboard casing (controllerboard version 2.0/2.1 with USB-C power) and rear exit of servo & steppermotor wiring).
render
* Bracket for case (USB-C version) mounting to the original rear Opentrickler steppermotor body.
* Cable management for use with Servogate mod to guide the servo wires out of sight and out of reach of the belts, steppermotors and Trickler tubes.

What is needed per part:
* Opentrickler casing: SHCS 4x M3x30, 4x M3 nut.
* Bracket for casing to house the controllerboard v2.0 with USB-C: 2x BHCS M3x10, 2x SHCS M3x12, 2x M3 nut + 2x Heatset insert M3x5x4 (to go into the side of 'rear_body.stl'.
* Cable management for Servogate wiring: SHCS 2x M3x14

Instructions cable management (new):
* First install the Servogate Trickler body (front assembly).
* Install the cable management part and during placement please guide the wires carefully to the right.
* Bolt down with the new SHCS.
* Install the rear trickler steppermotor bracket.

Instructions cable management (as an addition):
* Loosing the 4x SHCS from the rear trickler steppermotor bracket.
* Carefully move it backward to create space to guide the Cablemanagement part in between.
* Install the cable management part and during placement please guide the wires carefully to the right.
* Bolt down with the new SHCS.
* Slide back the rear trickler steppermotor bracket and thighten the 4x SHCS.

Have fun.

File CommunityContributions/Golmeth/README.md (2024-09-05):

# Golmeth's Mods

* [Lee Bottle Adapter](STL/LEE-adapter2-final.stl) replaced the hopper base with the adapter for the Lee hopper.

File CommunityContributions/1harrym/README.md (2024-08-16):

# 1harrym's Mod

* [Powder Hopper Water Bottle Adapter](STL/OpenTrickler_Waterbootle_Adapter.stl) replaced the hopper base with threaded adapter for the commonly available water bottle.

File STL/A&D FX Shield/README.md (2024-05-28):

# A&D FX Shield Print and Assembly Guide

The OpenTrickler is designed to be mounted to the A&D FX Shield if you're using the A&D fx-120/300i series of precision scales. 



## Print Guide

| Filename | Quantity | Remarks |
| --- | --- | --- |
| [cup_base_7mm.stl](cup_base_7mm.stl) | 1 | |
| [front_discharger_mount.stl](front_discharger_mount.stl) | 1 | |
| [pan_cover.stl](pan_cover.stl) | 1 | |
| [pan_cover_lid.stl](pan_cover_lid.stl) | 1 | |
| [powder_cup_body.stl](powder_cup_body.stl) | 1 | |
| [powder_cup_handle.stl](powder_cup_handle.stl) | 1 | |
| [rear_discharge_cup_ring.stl](rear_discharge_cup_ring.stl) | 1 | |
| [rear_discharge_mount.stl](rear_discharge_mount.stl) | 1 | |
| [rear_discharger_cup.stl](rear_discharger_cup.stl) | 1 | |
| [rear_discharger_sliding_door.stl](rear_discharger_sliding_door.stl) | 1 | |
| [scale_base_adapter_ring.stl](scale_base_adapter_ring.stl) | 1 | |
| [scale_pan_cover.stl](scale_pan_cover.stl) | 1 | |
| [scale_shield.stl](scale_shield.stl) | 1 | |
| [scale_weighing_pan_adapter.stl](scale_weighing_pan_adapter.stl) | 1 | |
| [trickler_adapter_plate.stl](trickler_adapter_plate.stl) | 1 | |
| [weighing_pan_27mm.stl](weighing_pan_27mm.stl) | 1 | See note below |

### How to Print Weighing Pan?

You **DO NOT** need to enable support to print the weighing pan. The slicer (using the OrcaSlicer as example) will automatically recognize the floating surface as bridge (or Overhang if you're using PrusaSlicer). The slicer will automatically reduce the speed and flow, and increase the fan speed to print mid air. 

print_weighting_pan_with_bridge

Using the [tutorial](https://help.prusa3d.com/article/poor-bridging_1802) to tune the slicer for better bridging performance. 

## BOM

| Name | Quantity | Remarks |
| --- | --- | --- |
| Heatset Inserts M3x5x4 | 15 | |
| M3x6 BHCS | 8 | |
| M3x12 SHCS | 4 | |
| M3x10 SHCS | 8 | |
| M3x8 SHCS | 7 | |

## Tools

* 2.0 mm hex driver

* 2.5 mm hext driver

## Assembly of Weighing Pan

weighing_pan_overview

### Inspection

Insert the [scale_weighing_pan_adapter.stl](scale_weighing_pan_adapter.stl) to the square groove of the A&D FX-120i/300i scale bottom down, make sure the adapter can be inserted to be groove and seat firmly. If not, you may need to re-print with more or less flow ratio. 

scale_to_weighing_pan_adapter_inspection

### Component Prep

Melt 1x heatset insert into the bottom side of the [cup_base_7mm.stl](cup_base_7mm.stl). Make sure the heatset insert seats flush with the bottom surface.

cup_base_install_heatset_insert

Melt 1x heatset insert into to the [scale_weighing_pan_adapter.stl](scale_weighing_pan_adapter.stl). Make sure the heatset insert seats flush with the top surface.

scale_to_weighing_pan_adapter_install_heatset_insert

### Assembly

Use 1x M3x6 BHCS to join the [weighing_pan_27mm.stl](weighing_pan_27mm.stl) with the [scale_weighing_pan_adapter.stl](scale_weighing_pan_adapter.stl).

mate_scale_adapter_with_weight_pan

Then use 1x M3x6 BHCS to join the [cup_base_7mm.stl](cup_base_7mm.stl) to the [weighing_pan_27mm.stl](weighing_pan_27mm.stl). 

mate_cup_base_with_weighing_pan

### Put some money in the pocket

You need to provide some coins in all 3 pockets to increase the overall weight of the [weighing_pan_27mm.stl](weighing_pan_27mm.stl) to reach the minimum weight of A&D FX-120i/300i. The stock weighing pan is measured about 100 grams. Coins are needed to add up to this weight. 

What coin to use? Below is the reference table. 

| Coin | Diameter | Weight | Minimum Quantity |
| --- | --- | --- | --- |
| New Zealand \$2 | 26.5 mm  | 10 g | 6 |
| Australia $1 | 25 mm | 9 g | 7 |
| Euro €2 | 25.75 mm | 8.5 g  | 7 |
| US $1 | 26.49 mm | 8.1 g  | 8 |

## Assembly of Poweder Cup

Powder cup assembly is straight forward. Two M3x6 BHCS are designed to be tapped into the [powder_cup_body.stl](powder_cup_body.stl) directly in order to join with the [powder_cup_handle.stl](powder_cup_handle.stl).

powder_cup_assembly

## Assembly of A&D FX Shield



### Component Prep

8x heatset inserts are to be melted into the plastic on both sides of the [scale_shield.stl](scale_shield.stl). 



### Assembly

Use 4x M3x12 SHCS to join [scale_base_adapter_ring.stl](scale_base_adapter_ring.stl), [scale_pan_cover.stl](scale_pan_cover.stl) and [scale_shield.stl](scale_shield.stl) together. 



Use 8x M3x10 SHCS to join the [trickler_adapter_plate.stl](trickler_adapter_plate.stl), with [front_discharger_mount.stl](front_discharger_mount.stl) and [rear_discharge_mount.stl](rear_discharge_mount.stl). Screws are to be
threaded to the bottom the OpenTrickler front and rear body. 



Use 4x M3x8 SHCS to join the trickler adapter assembly and scale shield assembly together. (The OpenTrickler body is hidden to for demonstration purpose).



## Assembly of Pan Cover

The pan cover is used to protect the pan from dust or accidental drops. The pan cover can be seamly
put onto the shield body when not used. 



### Component Prep

Melt 3x heatset inserts into the [pan_cover.stl](pan_cover.stl) from the top.



### Assembly

Install 2x M3x6 BHCS to the bottom of the [pan_cover.stl](pan_cover.stl). Do not over tighten those screws as they are designed to directly screw into the plastic. 



Use 3x M3x8 SHCS to join the [pan_cover_lid.stl](pan_cover_lid.stl) to the [pan_cover.stl](pan_cover.stl). 



## Assembly of Rear Discharge Cup

The discharge cup is used to help cleaning powder from the reservoir by catching remaining powder from the drainage hole. 



### Component Prep

Melt 2x heatset inserts into the [rear_discharge_cup_ring.stl](rear_discharge_cup_ring.stl). 



### Assembly

Use 2x M3x6 BHCS to join the [rear_discharge_cup_ring.stl](rear_discharge_cup_ring.stl) to the [rear_discharger_cup.stl](rear_discharger_cup.stl). 



Now you can slide the Rear Discharger Cup to the A&D FX Shield and finish the assembly. 

## Appendix A - Interface Drawing

If you're the designer and looking to port the A&D FX Shield to other precision scale, you could use the below interface drawing to design the adapter. 

interface_drawing

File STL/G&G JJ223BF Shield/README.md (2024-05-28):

# G&G JJ223BF Shield Print and Assembly Guide

> :warning: **The G&G JJ BF series scales are evaluated not suitable for OpenTrickler application. Please hold off before purchase!**
> The G&G JJ BF series scales has inconsistent weight refresh rate at small weight changes. The evaluation suggested the scale may take up to 10 seconds to register a kernel drop, for which nullify the PID control algorithm adopted by the OpenTrickler firmware. 

assembly_overview

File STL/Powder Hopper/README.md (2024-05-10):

# Powder Hopper Print and Assembly Guide



## Print Guide

| Filename | Quantity | Remarks |
| --- | --- | --- |
| [hopper_base.stl](hopper_base.stl) | 1 | The design includes large overhang (45 deg). You may need to reduce the print speed to archieve better surface finish. |
| [hopper_body_100mm.stl](hopper_body_100mm.stl) | 1 (optional) | Print in vase mode (no Z seam) with 0.8mm single wall thickness. You can select the part between 100, 150 and 200mm height body. <br>The height can be customized by scaling the part in Z direction. |
| [hopper_body_150mm.stl](hopper_body_150mm.stl) | 1 (optional) | Print in vase mode (no Z seam) with 0.8mm single wall thickness. You can select the part between 100, 150 and 200mm height body. |
| [hopper_body_200mm.stl](hopper_body_200mm.stl) | 1 (optional) | Print in vase mode (no Z seam) with 0.8mm single wall thickness. You can select the part between 100, 150 and 200mm height body. |
| [hopper_cap.stl](hopper_cap.stl) | 1 | |
| [rear_body_interface.stl](rear_body_interface.stl) | 1 | |

## BOM

| Name | Quantity | Remarks |
| --- | --- | --- |
| M3x8 BHCS | 1 | |
| Shim Washer | 2 | OD=6mm, ID=3mm, Thick=0.5mm |

## Tools

* 2.0 mm hex driver

### Assembly

Stack the [hopper_base.stl](hopper_base.stl) to the [rear_body_interface.stl](rear_body_interface.stl). Note the travel limiter should sit in the groove and the valve is in the "open" position. 



Stack 2x M3 washer to the [rear_body_interface.stl](rear_body_interface.stl) pocket, then thread the M3x8 BHCS directly to the [hopper_base.stl](hopper_base.stl). Don't over tighten the screw and make sure the hopper base can rotate (with some resistance) between ON and OFF position. 



Lastly, slide the powder hopper to the top of the rear body. Make sure to push the powder hopper all the way in. The [rear_body_interface.stl](rear_body_interface.stl) should sit flush with the rear body assembly.



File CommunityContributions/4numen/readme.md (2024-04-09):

**OpenTrickler addons:**
Phone holder & front assembly door combo. Makes replacement of screen with phone more convenient.
Prints without supports

**JJ100B Workflow enhancements:**

1. Bumper preventing bump into scale plate, should help the scales last longer. Makes placement of the cup smoother and helps get "zero" quicker. You will need one M3 10mm tapered screw to attach ring basee to the bumper.
2. Scale plate with press-on possitioning ring. Helps possition the cup on the plate consistently - quicker. The ring shoul press on the ring if not, you might need to play with x & Y scale +/- 0,01%

**Bumper picture:**              

Bumper

**Phone holder picture:**

Phone_holder

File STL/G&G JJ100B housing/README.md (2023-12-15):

# OpenTrickler for G&G JJ100B Housing

assembly_view

Note: The author [@SWT-tech](https://github.com/SWT-tech) forbids the use of design for commerical purposes. Please read [LICENSE.txt](LICENSE.txt) for details.

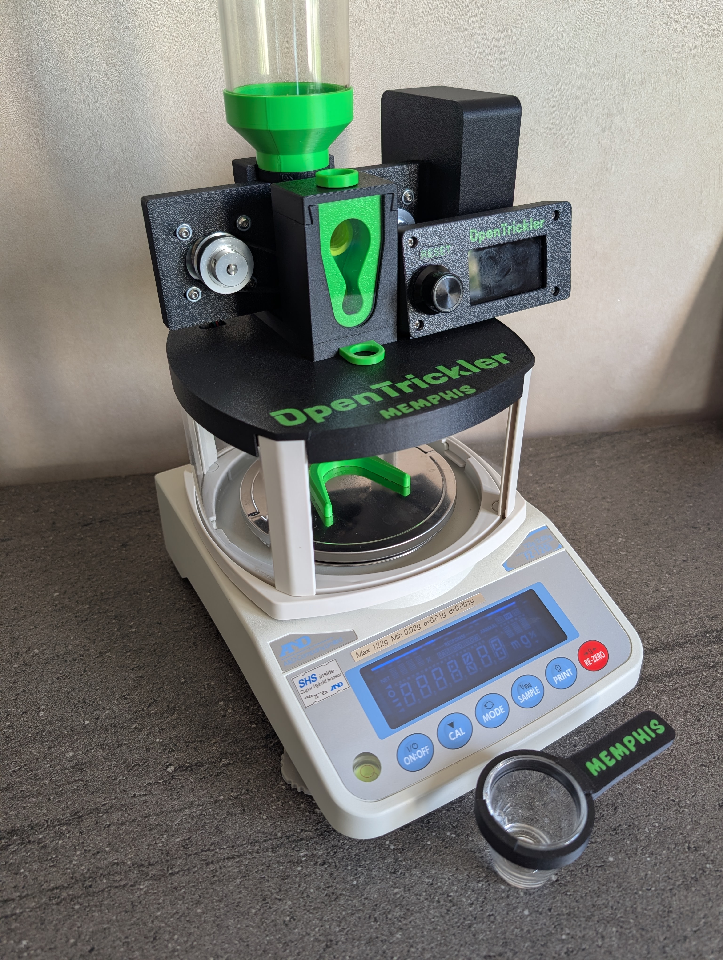
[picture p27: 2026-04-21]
CommunityContributions/Memphis/V2/ressources/Overview_1.jpg

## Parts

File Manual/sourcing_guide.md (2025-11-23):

# Sourcing Guide

This document provides information regarding the self sourcing guide for aftermarket parts. 

✅ indicates parts that are verified to be compatible with the OpenTrickler system. 

## Things for OpenTrickler Controller

> [!Note]
> You can purchase the board directly from Mellow 3D and ship worldwide now. 
> LINK: https://www.aliexpress.com/item/1005008080766173.html

You could find details for Pico Motor Expansion Board from the [repository](https://github.com/eamars/RaspberryPi-Pico-Motor-Expansion-Board).

### (For OpenTrickler Controller v1) 12/24V Power Supply

You can use either 12V or 24V power supply. It is recommended to have minimum 2A output capacity to avoid any potential brown out when the motors draw too much current. Belows are recommended power supplys. 

* [Meanwell LRS-50-24 from Digikey](https://www.digikey.co.nz/en/products/detail/mean-well-usa-inc/LRS-50-24/7705048)

### (For OpenTrickler Controller v2) USB-C PD Power Supply

* [VOLTME 30W Type C Charger](https://www.aliexpress.com/item/1005004696508238.html)

### 2mm Pitch Jumper Cap

You will need 3x 2mm pitch female jumper per board. 

* [Aliexpress](https://www.aliexpress.com/item/3256803974952256.html)
* [RS-Online](https://nz.rs-online.com/web/p/jumpers-shunts/6742404)

### Raspbery Pi Pico 2W

The Pico 2W (with wireless) can be purchased according to the [Rasperry Pi offial site](https://www.raspberrypi.com/products/raspberry-pi-pico-2/?variant=pico-2-w). 

You can choose with or without the GPIO headers. If no GPIO header version is selected then you need to source and solder the 2x 40 single row 2.54mm pitch header yourself. 

Note: The first gen Pico W is supported but not recommended to use anymore due to the potential software incompatibility. 

#### 2.54mm pitch header for Pico 2W

You can buy single row of 40 pin header and cut into 2x 20 pin header yourself. Below are recommended sources. 

* ✅[LCSC](https://www.lcsc.com/product-detail/_ZHOURI-_C2977586.html)
* [Aliexpress](https://www.aliexpress.com/item/3256805561549792.html)

Additional 3 pin header can be soldered to the front of the Pico W to pair with [PicoProbe](https://github.com/raspberrypi/picoprobe) for advanced debugging/developing purpose.

#### MicroUSB cable for Pico 2W

Any MicroUSB data cable can be used to program the Pico W firmware. Those cable were commonly used for last generation of cell phones. Below are example parts. 

* [Aliexpress](https://www.aliexpress.com/item/3256805656009583.html)

### Servo Motors

Full metal and 180 deg rotation angle ones are recommended. 

* [MG90s](https://www.aliexpress.com/item/1005004550692203.html)

### RS232 Cable (with DB9 header)

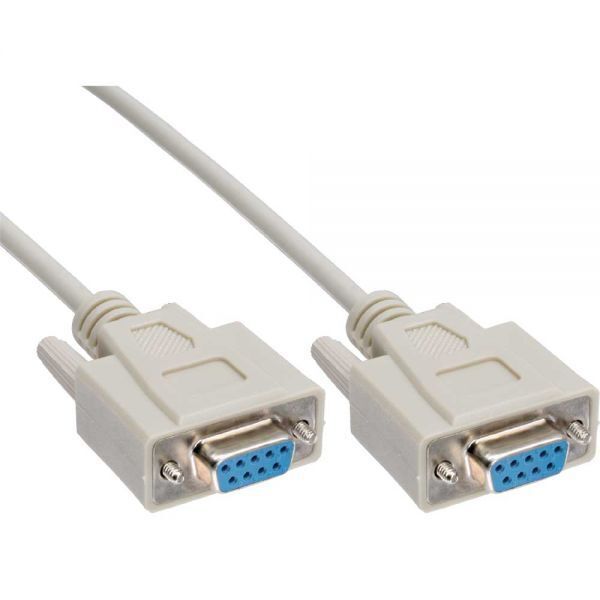
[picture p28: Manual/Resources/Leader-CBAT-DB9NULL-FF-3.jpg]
db9 cable


**A&D FX-120i/300i** You will need a **female to female** DB9 cable. 
**G&G JJ100B** You will need a **male to female** DB9 cable.
You can use either straight-through or NULL-modem cable. Subject to the type of the cable you will need to insert the [2mm pitch jumper](#2mm Pitch Female Jumper) accordingly. Below are example parts. 

* [Aliexpress](https://www.aliexpress.com/item/3256805572553474.html)
* [Aliexpress](https://www.aliexpress.com/item/3256805240818006.html)

### Stepper Motor Driver

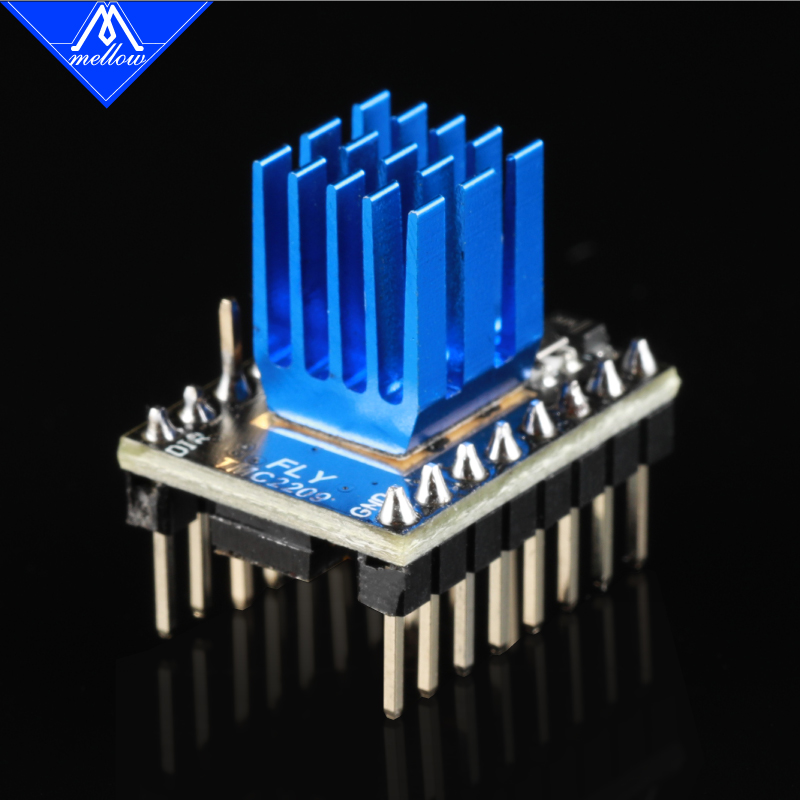
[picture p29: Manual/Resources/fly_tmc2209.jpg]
tmc2209


You will need two TMC 2209 stepper driver per board. 

Subject to the specific assumption of the StepStick wiring, the TMC2209 module from certain manufacturers are recommended. 

*Please note there is no standard pin out for TMC2209 StepStick modules therefore please stick to the recommended parts.*

* ✅ Fly TMC2209 [https://www.aliexpress.com/item/1005001877899893.html](https://www.aliexpress.com/item/1005001877899893.html)
* ✅ BigTreeTech TMC2209 [https://www.aliexpress.com/item/33029587820.html](https://www.aliexpress.com/item/33029587820.html) 
  **The listing includes both TMC2208 and TMC2209. Make sure to select TMC2209**.
* BigTreeTech TMC2209 via [Official Site](https://biqu.equipment/collections/driver-board/products/bigtreetech-tmc2209-stepper-motor-driver-for-3d-printer-board-vs-tmc2208).

### Mini 12864 Display with Controller

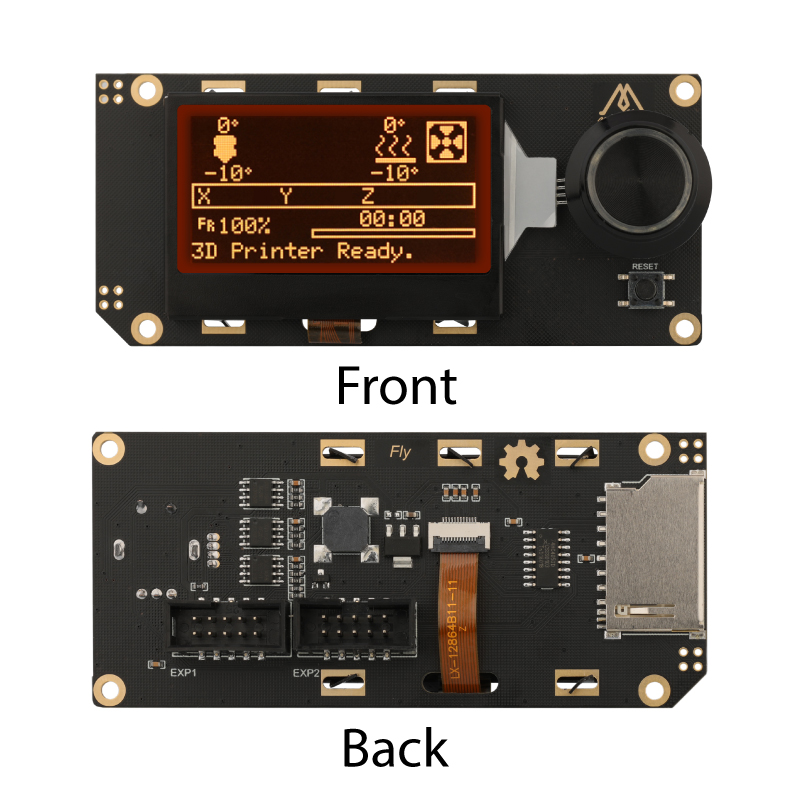
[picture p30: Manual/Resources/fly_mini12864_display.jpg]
fly_mini12864


Subject to the implementation of [Motor Expansion Board](https://github.com/eamars/RaspberryPi-Pico-Motor-Expansion-Board), The mini 1286 display from certain manufactorers are recommended.

*Please note there is no standard pin out for mini 12864 displays therefore please stick to the recommended parts.*

* ✅ Fly mini 12864 [https://www.aliexpress.com/item/1005003579276633.html](https://www.aliexpress.com/item/1005003579276633.html)
* ✅ BigTreeTech mini 12864 [https://www.aliexpress.com/item/1005005114662084.html](https://www.aliexpress.com/item/1005005114662084.html)

## Things for OpenTrickler Hardware Assembly

### Bearings

#### 6801-2RS or 6801ZZ

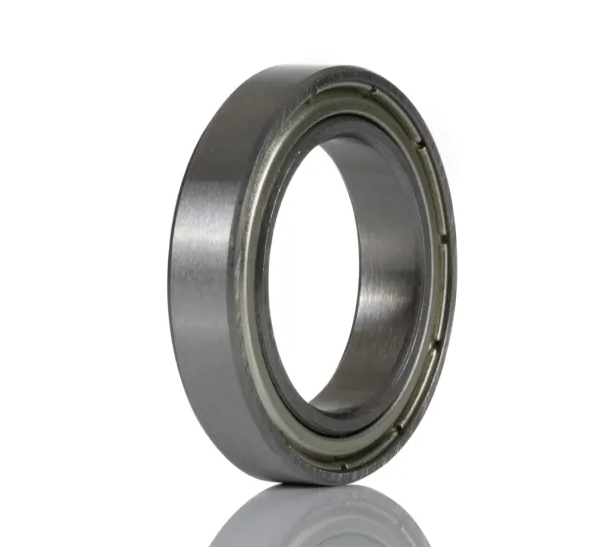
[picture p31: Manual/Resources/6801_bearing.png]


You can find the bearing from [https://www.aliexpress.com/item/4000120762936.html](https://www.aliexpress.com/item/4000120762936.html)

✅ Select 6801-2RS 12X21X5mm

*"In summary, the primary difference between "-ZZ" and "-2RS" lies in the type of sealing or shielding they have. "-ZZ" has metal shields on both sides, while "-2RS" has rubber seals on both sides."* - by ChatGPT

You will need 2x 6801 bearing per OpenTrickler Assembly.

#### 6804-2RS or 6804ZZ

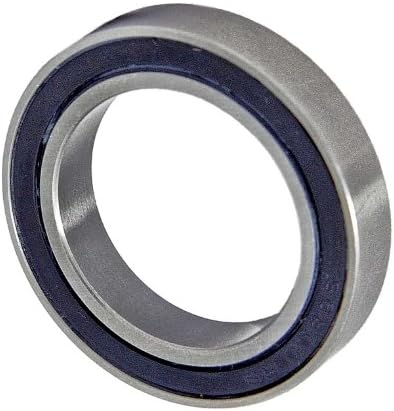
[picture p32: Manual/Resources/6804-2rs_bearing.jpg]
6804_bearing


You can find the bearing from [https://www.aliexpress.com/item/4000120762936.html](https://www.aliexpress.com/item/4000120762936.html)

✅ Select 6804-2RS 20x32x7mm 

You will need 2x 6804 bearing per OpenTrickler Assembly.

### Nema 17 Stepper Motors

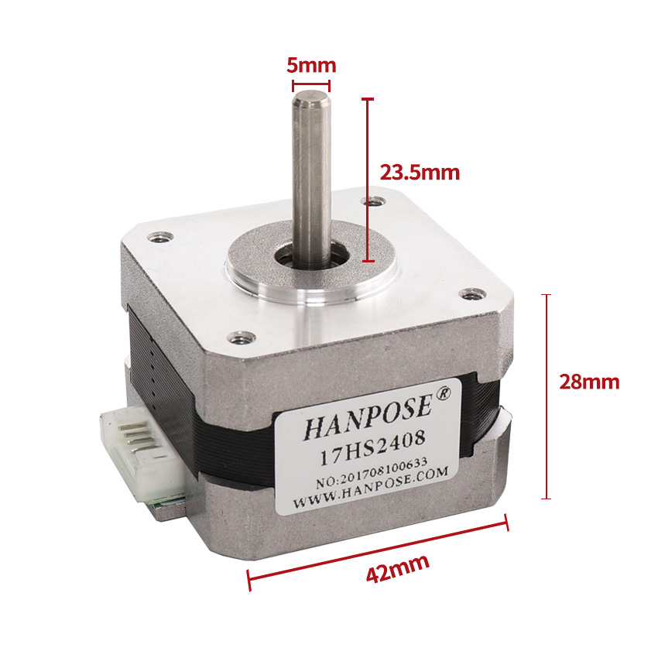
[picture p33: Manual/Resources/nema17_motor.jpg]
nema17_motor


Any bipolar NEMA17 (42mm) stepper motor will work. The only thing you need to worry about is the output shaft. The output shaft need to be 5mm in diameter and longer than 20mm measured from the surface. 

* Hanpose 42x24mm [https://www.aliexpress.com/item/1005005195056354.html](https://www.aliexpress.com/item/1005005195056354.html)

You will need 2x stepper motors per OpenTrickler Assembly.

### GT2 Belts

Both belts can be 3d printed. However if you're not feeling good to print those in TPU, you can also buy the aftermarket part. 

*The aftermarket close loop belts needs to be 1 teeth longer than the printed belt for easy to install purpose.*

#### Coarse Trickler Tube Belt

[https://www.aliexpress.com/item/1005003420172630.html](https://www.aliexpress.com/item/1005003420172630.html)

* 174mm (87 teeth). 

#### Fine Trickler Tube Belt

[https://www.aliexpress.com/item/1005003420172630.html](https://www.aliexpress.com/item/1005003420172630.html)

* 166 mm (83 teeth)

### 40 Teeth GT2 Timing Pulley

Both pulleys can be 3d printed. However if you're not feeling good to print those yourself, you can find the aftermarket parts. Below are example parts. 

* 5mm bore, for belt width 6mm [https://www.aliexpress.com/item/1005002843440540.html](https://www.aliexpress.com/item/1005002843440540.html)

You will need 2x per OpenTrickler Assembly.

### Heatset Inserts

The heatset inserts with corresponding quantity can be found from the [assembly manual](assembly.md)

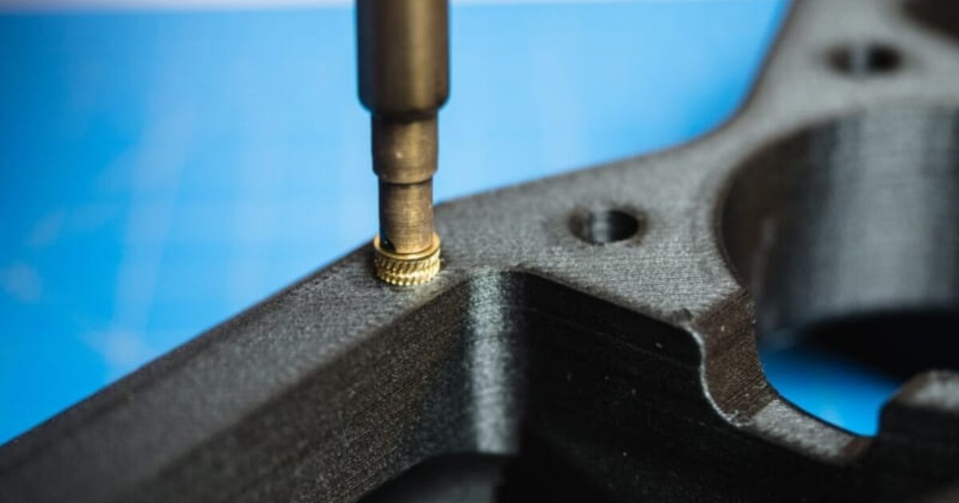
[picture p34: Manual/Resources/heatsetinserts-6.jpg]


The dimension of the heatset inserts can be referenced as follow:

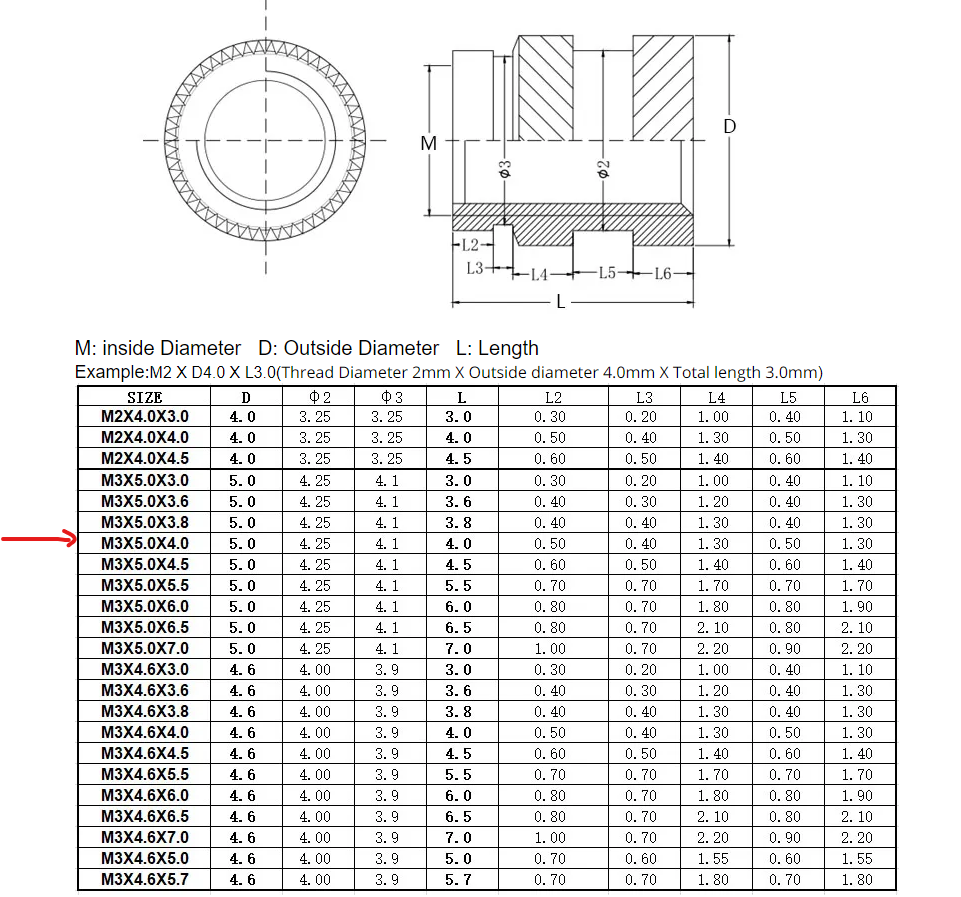
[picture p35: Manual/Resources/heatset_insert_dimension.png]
heatset_insert_dimension


The heatset inserts (M3xD5xL4) are commonly used in the OpenTrickler assembly to join two plastic parts. Below are recommended parts

* ✅[Aliexpress](https://www.aliexpress.com/item/4000232858343.html)

### Assorted Screws

The screws with corresponding quantity can be found from the [assembly manual](assembly.md)

**Screws explained:** 
Socket Head Cap Screw (SHCS) The standard for socket cap screws. It features a cylindrical head with a recessed hex. It can be installed into a counter-bored hole or above the surface of the material.

shcs

Button Head Socket Cap Screw (BHCS) Features a domed head with a recessed hex. The head is wider and lower profile than a standard Socket Head Cap Screw.

bhscs

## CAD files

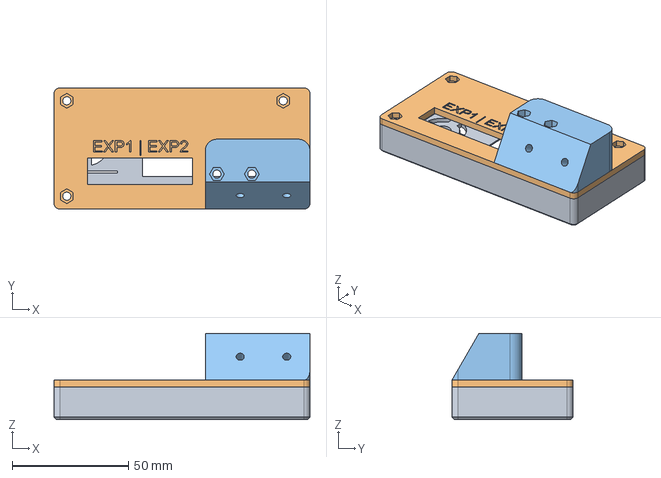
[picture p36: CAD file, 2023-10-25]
CommunityContributions/dirtbit/CAD/Display_Assy.step
110.0 x 52.0 x 37.0 mm

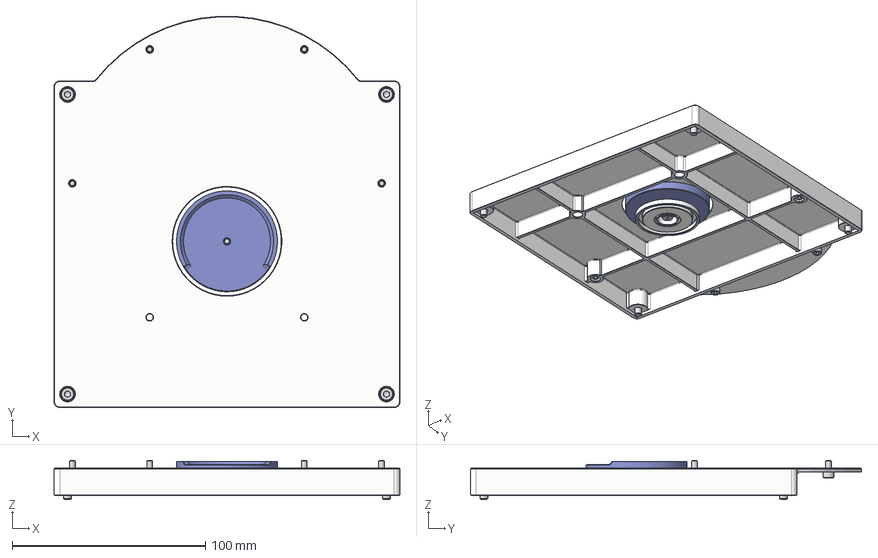
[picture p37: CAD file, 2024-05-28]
CAD/gng_jj223bf_base_assembly.step
179.0 x 202.4 x 20.2 mm
g&g_weighing_pan_dia_reducer
g&g_scale_weighing_pan_adapter
cup_base
M3 Threaded Insert
M3x8 FHCS
M3x12 SHCS x 2
M3x6 SHCS x 2
M4x12 SHCS x 4

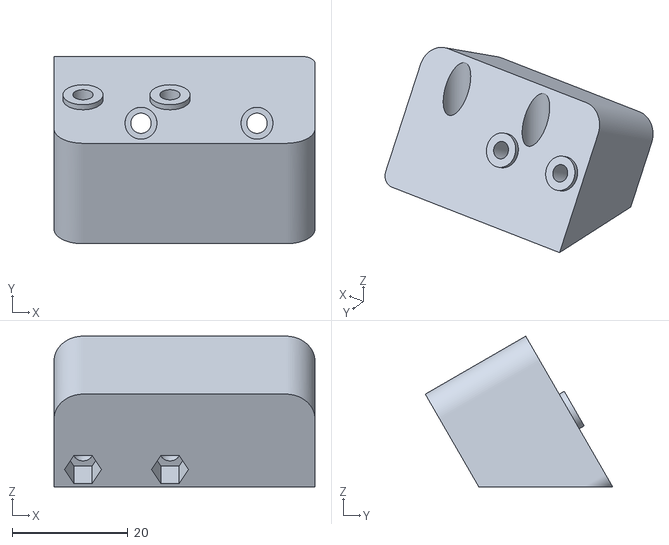
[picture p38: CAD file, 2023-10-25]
CommunityContributions/dirtbit/STL/Display_Assy_bracket.stl
45.0 x 32.3 x 26.0

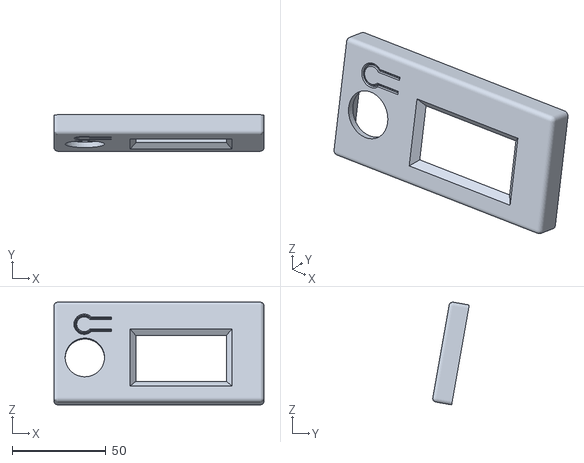
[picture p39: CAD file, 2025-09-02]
CommunityContributions/Memphis/STL/display_assy_front.stl
112.2 x 19.5 x 54.9

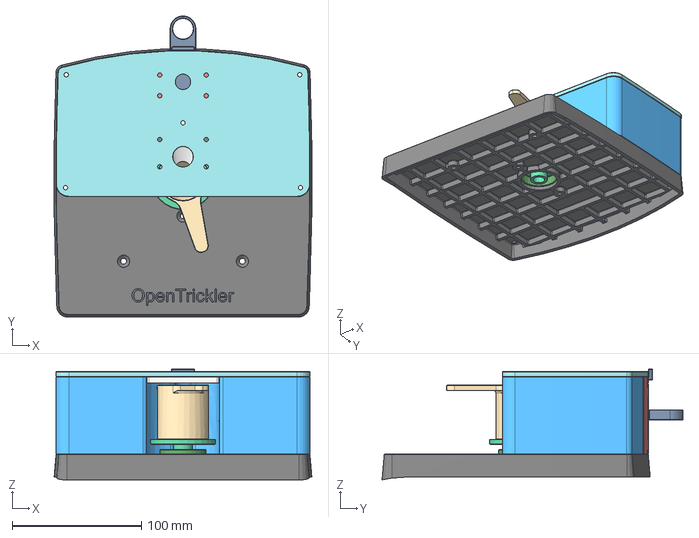
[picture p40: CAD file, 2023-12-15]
CAD/JJ100B_ASSEMBLY.stp
199.7 x 233.2 x 86.0 mm

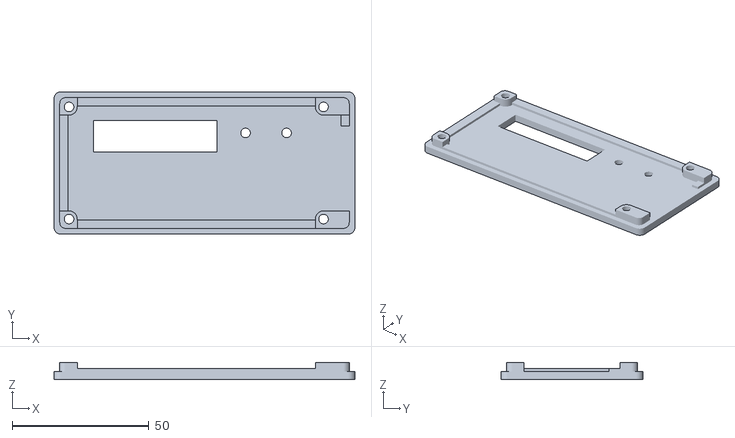
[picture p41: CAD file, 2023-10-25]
CommunityContributions/dirtbit/STL/Display_Assy_body.stl
110.0 x 52.0 x 6.30

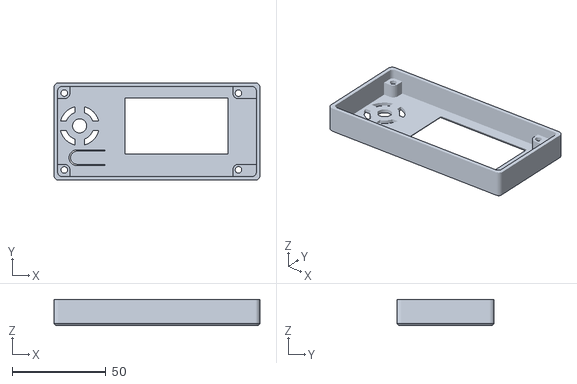
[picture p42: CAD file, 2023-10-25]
CommunityContributions/dirtbit/STL/Display_Assy_front.stl
110.0 x 52.0 x 14.0

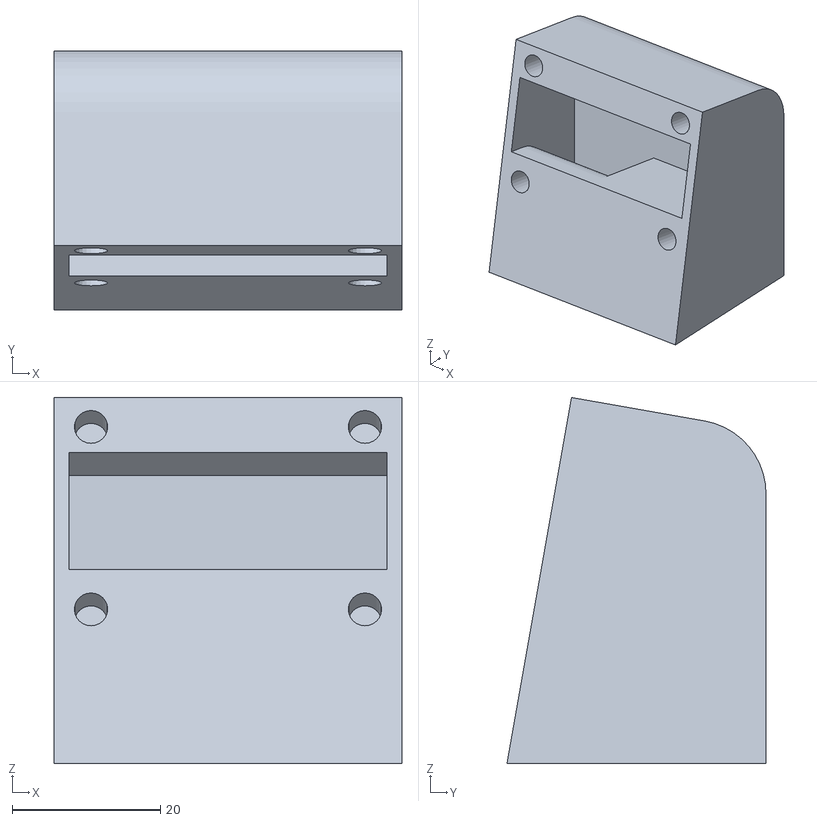
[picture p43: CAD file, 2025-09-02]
CommunityContributions/Memphis/STL/display_assy_bracket.stl
47.0 x 35.0 x 49.4

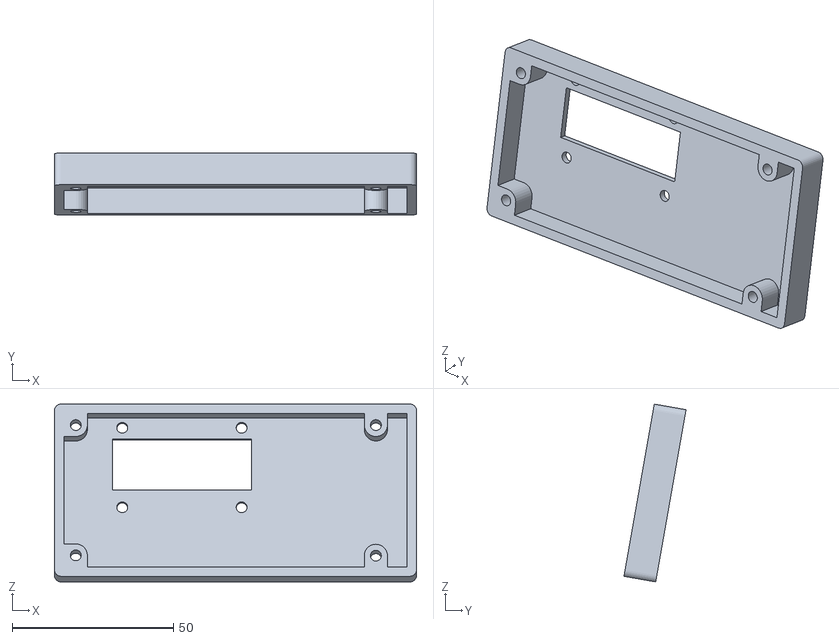
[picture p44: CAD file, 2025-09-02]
CommunityContributions/Memphis/STL/display_assy_body.stl
112.2 x 19.3 x 55.1

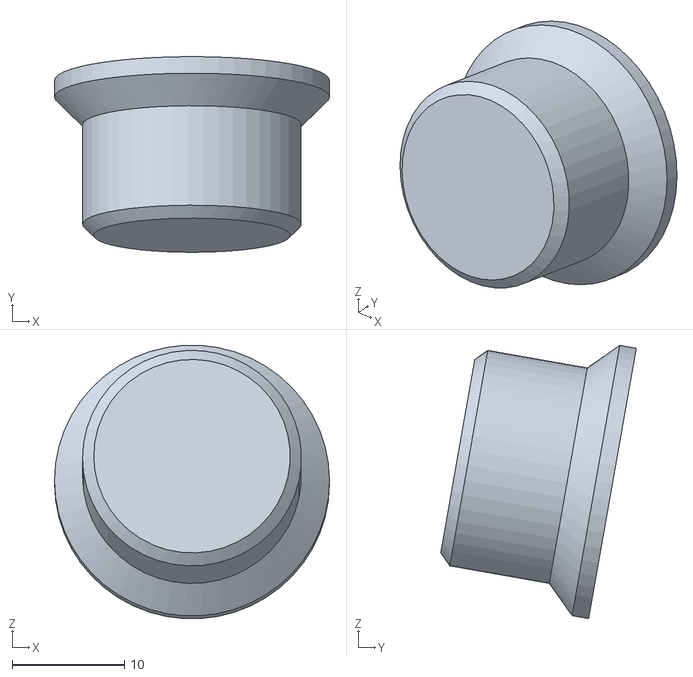
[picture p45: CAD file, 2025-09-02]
CommunityContributions/Memphis/STL/display_assy_button.stl
24.5 x 17.4 x 24.3

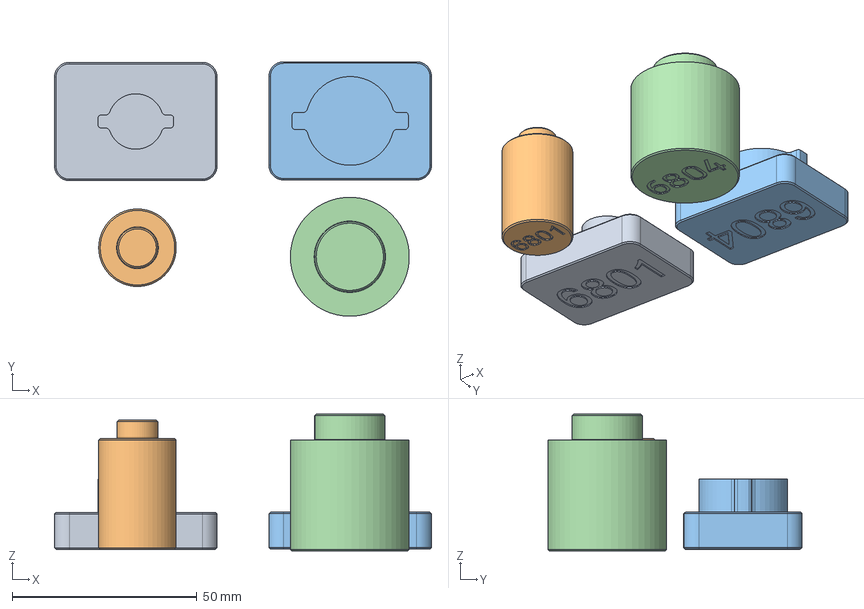
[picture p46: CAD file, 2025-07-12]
CAD/bearing_helpers.step
102.0 x 68.9 x 37.0 mm
6801_bearing_eject_helper
6801_bearing_press_helper
6804_bearing_eject_helper
6804_bearing_press_helper

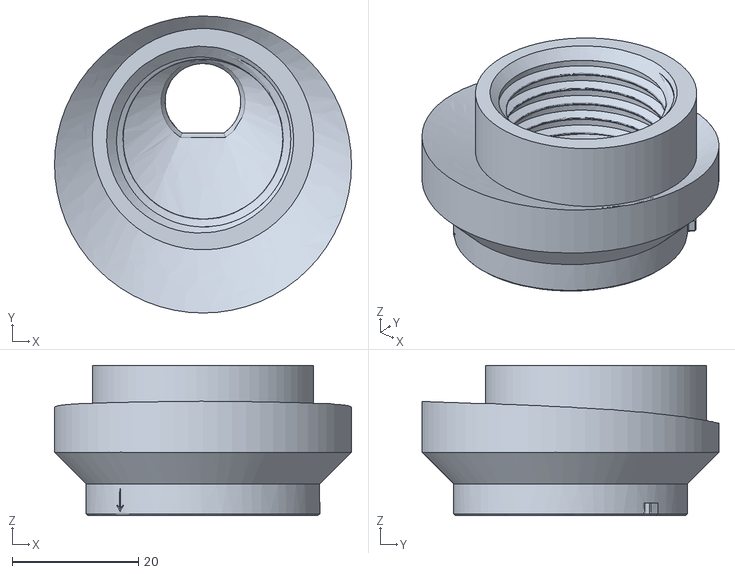
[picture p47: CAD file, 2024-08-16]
CommunityContributions/1harrym/STL/OpenTrickler_Waterbootle_Adapter.stl
47.0 x 47.0 x 23.8

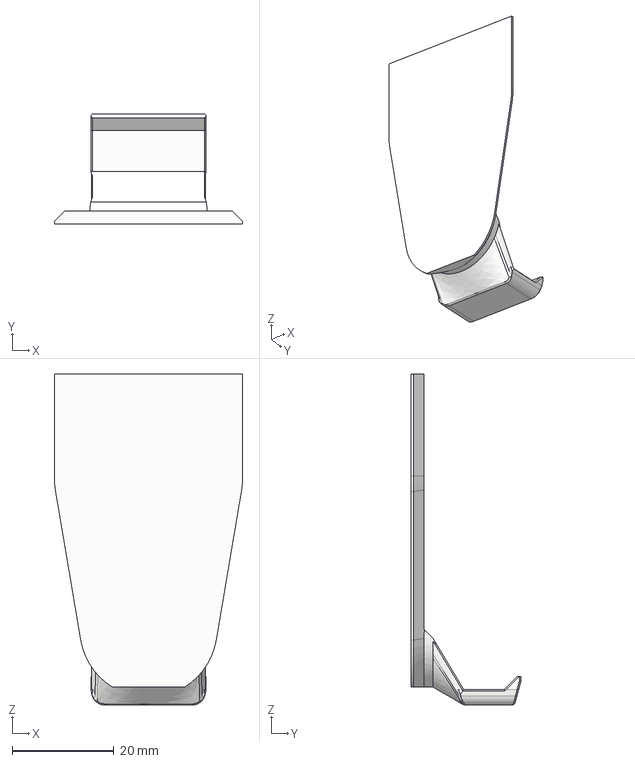
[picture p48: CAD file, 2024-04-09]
CommunityContributions/4numen/CAD/Phone_holder v1.step
37.0 x 21.5 x 65.0 mm

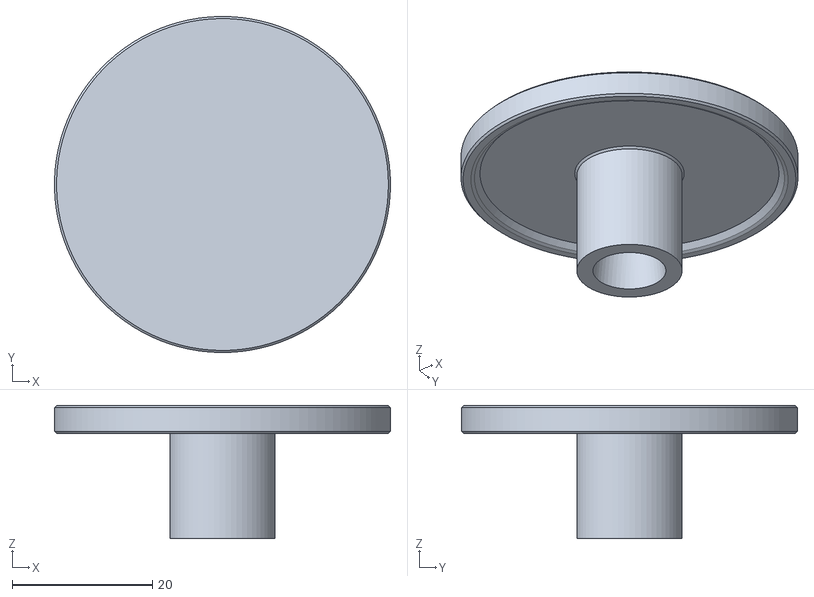
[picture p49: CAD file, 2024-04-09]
CommunityContributions/4numen/STL/JJ100B_ScalesPlate.stl
48.0 x 48.0 x 19.0

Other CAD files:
CommunityContributions/Crayons82/Step Files (CAD)/Base/BASE.step
CommunityContributions/Crayons82/Step Files (CAD)/Front body components/DUMP SHIELD.step
CommunityContributions/Crayons82/Step Files (CAD)/PCB board components/PCB FRONT COVER (1).step
CommunityContributions/Crayons82/Step Files (CAD)/Powder hopper components/POWDER TUBE.step
CAD/50g_weight_holder.step
CAD/A&D FX Shield.step
CAD/and_fx_scale_lid.STEP
CommunityContributions/4numen/CAD/JJ100B_Bumper v1.step
CommunityContributions/4numen/STL/JJ100B_Bumper.stl
CommunityContributions/4numen/STL/JJ100B_PossitioningRing.stl
CommunityContributions/4numen/STL/JJ100B_RingWithBumperBase.stl
CommunityContributions/4numen/STL/Phone_holder.stl
CommunityContributions/Crayons82/F3D (Fusion 360)/Fine tickler.f3d
CommunityContributions/Crayons82/F3D (Fusion 360)/OPEN TRICKLER V3.f3d
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

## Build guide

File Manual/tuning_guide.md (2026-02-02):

# Tuning Guide for Powder Profile

## Stop Thresholds

Stop thresholds are defined under Charge Mode -> Coarse/Fine Trickler Stop Threshold. The value are unitless. The unit should be tuned based on the unit reported by the scale. By default all values are designed for grain (gr). 

The coarse trickler stop threshold should be set around 3 to 5 gr, depending on the size of the kernel. 

The fine trickler stop threshold should be set to the accuracy of the scale. For example, the A&D FX-300i has accuracy of 0.001g or 0.02gr. In this case you should set to 0.02 gr stop threshold for best performance and accuracy. 

## Profile

The OpenTrickler controller is built based on the [Proportional-Integral-Derivative (PID) Controller](https://en.wikipedia.org/wiki/Proportional%E2%80%93integral%E2%80%93derivative_controller). Thus the Tuning Methods for a PID applies for the OpenTrickler. Except, the overshoot is unacceptable for which translate to the overthrow. 

The Coarse Trickler should be tuned separately from the fine trickler. Below is the effect of Kp, Ki and Kd to the system. 

| Parameter | Raise Time | Overshoot | Settling Time | Steady State Error | Stability |
| --- | --- | --- | --- | --- | --- |
| Kp | Decrease | Increase  | Small change  | Decrease | Degrade |
| Ki | KEEP AT 0 | KEEP AT 0 | KEEP AT 0 | KEEP AT 0 | KEEP AT 0 |
| Kd | Little change | Decrease  | Decrease | Theoretically no change | Improve if Kd is already low |

### Tuning Coarse Trickler

1. Start with Kp, Ki and Kd at 0. 

2. Increase Kp until the Coarse Trickler will overthrow beyond the Coase Trickler stop threshold. 

3. Keep Ki at 0 at all time. 

4. Increase Kd to reduce the overthrow to an acceptable threshold. 

The tuning goal is to reduce the Coarse Trickler operating time below 10 seconds. 

### Tuning Fine Trickler

1. Start with Kp, Ki and Kd at 0. 

2. Increase Kp until the Fine Trickler will overthrow beyond the charge weight. 

3. Keep Ki at 0 at all time.

4. Increase Kd to eliminate the overthrow to an acceptable threshold (for example, 1/15 overthrow). 

The tuning goal is to reduce the overall operating time below 15 seconds.

Remember to save the powder profile once you've found the optimal values. 

# References

[Tuning Methods of A PID Controller | CTRL ALT FTC](https://www.ctrlaltftc.com/the-pid-controller/tuning-methods-of-a-pid-controller)

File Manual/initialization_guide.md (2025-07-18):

# OpenTrickler Initialization Guide

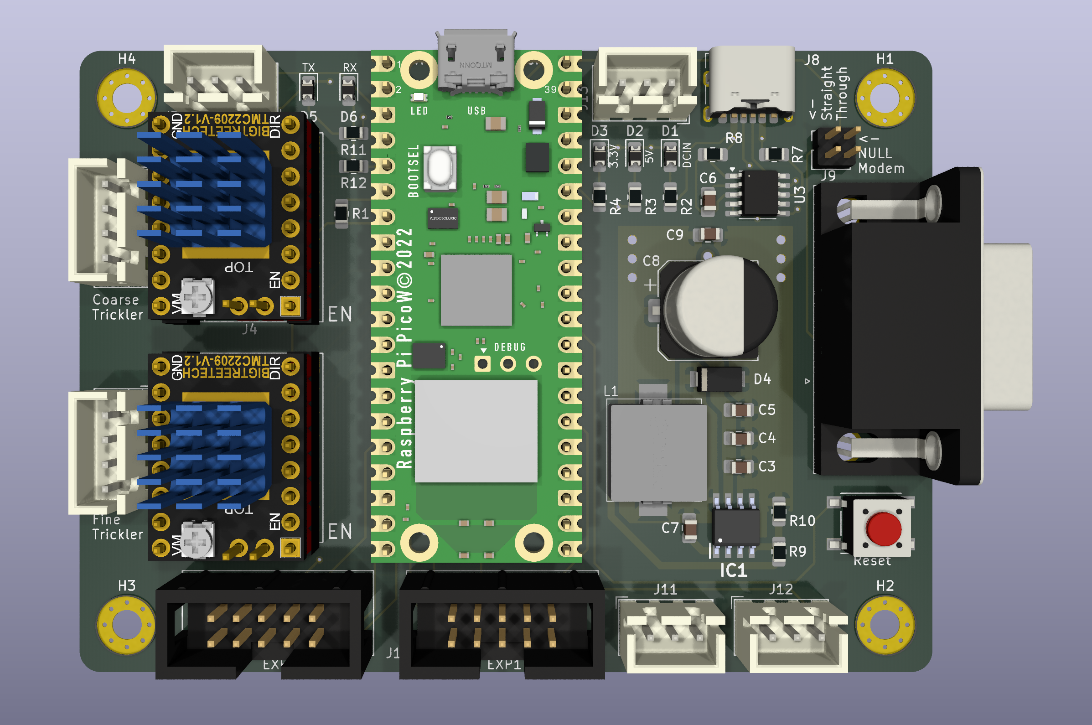
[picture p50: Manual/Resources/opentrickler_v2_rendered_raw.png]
final_product


## Pre-requisite

Below are pre-requisite steps you need to follow before continue.

1. [OpenTrickler assembly](assembly.md)

2. [Firmware deployment](https://github.com/eamars/OpenTrickler-RP2040-Controller/blob/main/manuals/firmware_update_via_usb.md)

3. Make sure you have everything prepared from [Sourcing Guide](sourcing_guide.md)

> [!IMPORTANT]  
> Below instructions are for OpenTrickler Controller v2.x. You can tell the board revision by inspecting the silkscreen. 

### RS232 Cable Type Select

To match the type of RS232 cable (with DB9 header), you need to select between the straight through wiring and null modem wiring with J9. 

[*What is NULL modem and straight through?*](https://www.decisivetactics.com/support/view?article=crossover-or-null-modem-vs-straight-through-serial-cable)

- NULL Modem: Connect two jumpers horizontally using 2x jumpers. 
- Straight Through: Connect two jumpers vertically using 2x jumpers. 

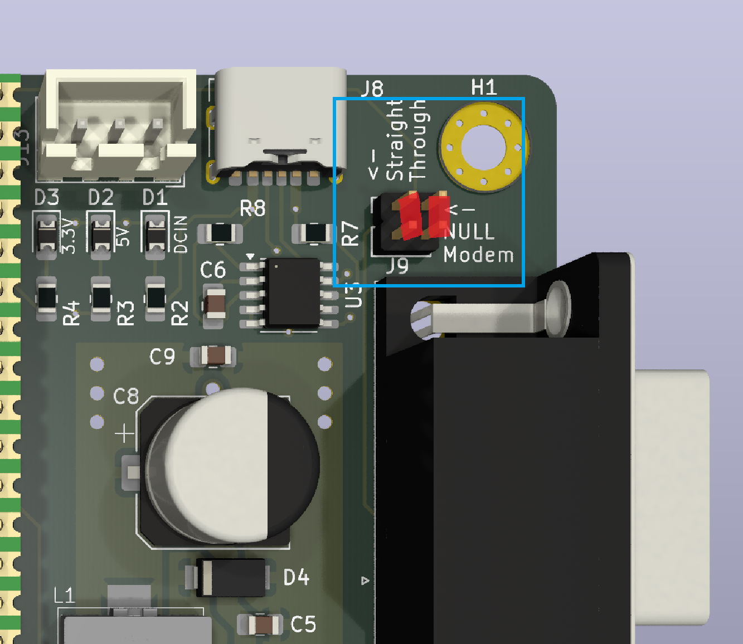
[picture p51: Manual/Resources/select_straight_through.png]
select_straight_through Straight Through Configuration


## Install Plug-in Components

### Install Raspberry Pico W

If your Raspberry Pico W doesn't come with headers pre-soldered, you will need to solder 2x 20 pin headers (2.54mm pitch) to the Pico W, then insert to the socket. Make sure the mini USB port is pointing towards the edge of the board. 

*Tips: Insert the 2x 20 pin header to the socket first, then solder pins to the Pico W will save your effort to line everything up.*

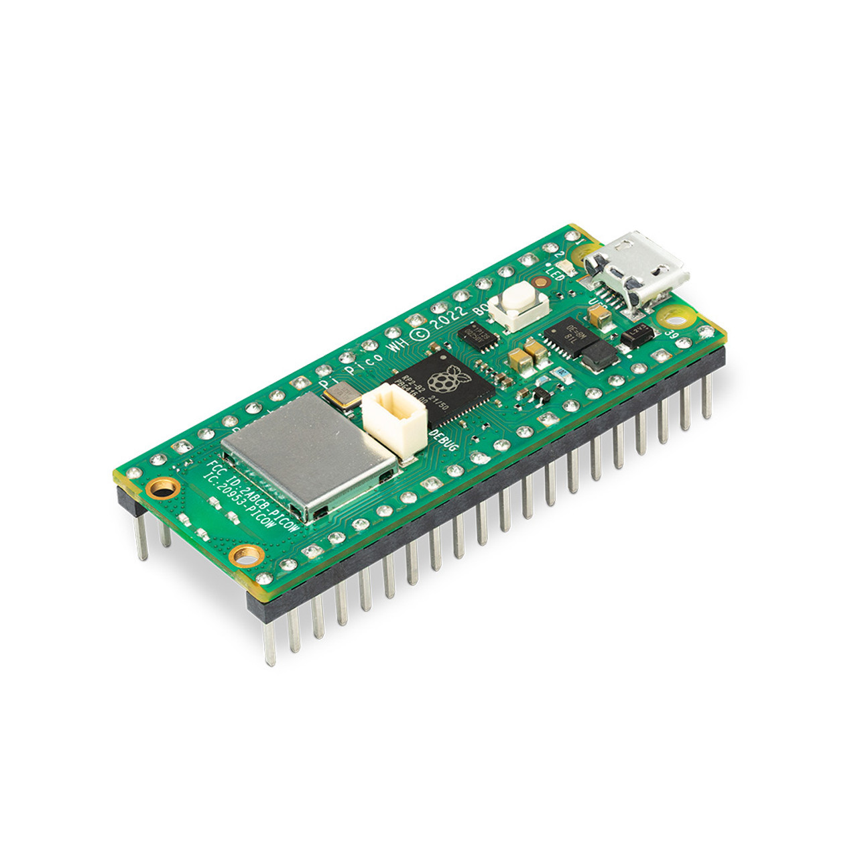
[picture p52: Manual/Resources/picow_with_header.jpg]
picow_with_header


### Install Stepper Motor Driver

Stepper motor drivers need to be inserted with specific orientation. Failed to do so will result in permanent damage to the board and the stepper motor driver. Make sure both VM and EN are lined up with the footprint from the board. 

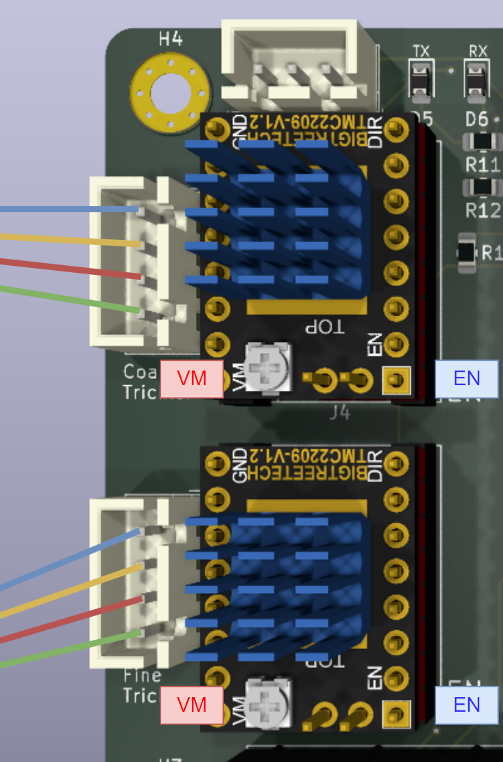
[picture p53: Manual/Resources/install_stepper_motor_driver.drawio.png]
install_stepper_motor_driver


## Wiring

It is time to wire everything up. Before turning on the power, double check the connection and placement of components. 

overview

**Notes**

- If you happen to use the Fysetc mini 12864 display, you may need to flip both EXP1 and EXP2 upside down (notch to the opposite side) due to the mirrored PIN out.
- There is no standard colour code, or the PIN order for the stepper motor cable. We will get into the stepper motor wiring and diagnose later.
- Pay special attention to the placement of power supply cable, Pico W and stepper motor drivers. Incorrect installation of those components may result in permanent damage to those components.

## Initial Startup Checks

It is time to power the board up! You may proceed if there is no visible [magic smoke](https://en.wikipedia.org/wiki/Magic_smoke).

### Inspect LED

There are 3x LEDs on the board and one on the Pico W. See the definition from the diagram below. You're supposed to see all power related LEDs (3.3V, 5V and 12V) turned on. The green LED (WiFi indication) on the Pico W is suppose to blink at 1Hz/s (If you already have the firmware loaded. Otherwise see the pre-requisite section above). 

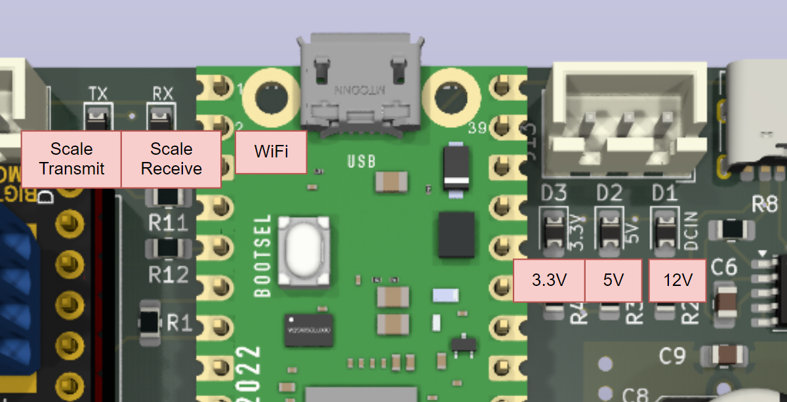
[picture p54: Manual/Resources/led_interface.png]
led_status


### Inspect Screen

You should be able to see the OpenTrickler menu from the screen, with back lights turned on. The two RGB LEDs underneath the rotary button is also supposed to emit white light. 

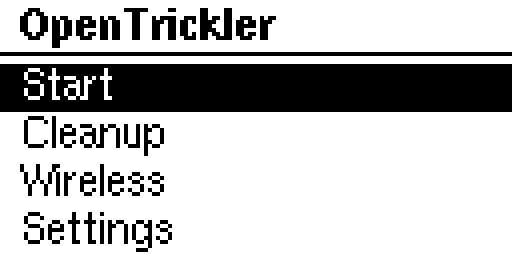
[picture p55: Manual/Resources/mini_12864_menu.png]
mini_12864_menu


Troubleshooting

* If the screen shows blank but there is backlight, you may need to press the RESET button on the board and check again. 
* If the screen shows blank and no backlight, you may need to check the EXP1 and EXP2 wiring. 
* If you have any doubt, join our discord and ask for help. 

### Connect to WiFi

You will need to follow [Connect to Wireless](https://github.com/eamars/OpenTrickler-RP2040-Controller/blob/main/manuals/connect_to_wireless.md) procedure to connect the Pico W to your home wireless and gain the access to the advanced configuration manual from the web interface. 

### Inspect Rotary Buttons

Subject to the vender of mini 12864 display, the rotary button direction can be interpreted in opposite direction. The designed direction is, when you rotate the nub clockwise, the menu cursor is suppose to move downwards. 

If the cursor moves in the opposite direction, you can correct it by login to the web interface, select "Settings" -> Buttons" and set "Yes" of the "Inverted Rotary Button Direction" option. 

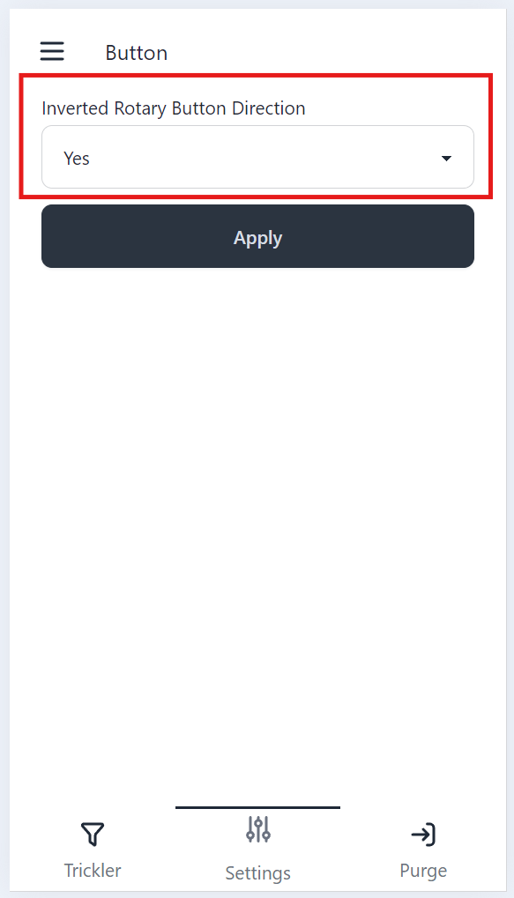
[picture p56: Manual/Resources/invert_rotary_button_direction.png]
invert_rotary_button_direction


You will need to save the settings to the EEPROM and reboot. 

### Inspect Motors

A quick way to validate the function of motors is to use Cleanup mode. 

*The cleanup mode is designed to clear the remaining powder left in the tube.*

**Steps:**

1. From the main menu, rotate the button until the cursor points to the "Cleanup", press the button downwards to continue.

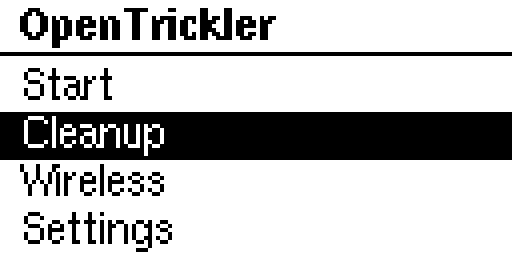
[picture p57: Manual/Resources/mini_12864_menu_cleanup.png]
mini_12864_menu_cleanup


2. You will then see the warning page. Make sure there is no powder in the reservoir, then rotate the button to "Next", press the button downwards to continue.  

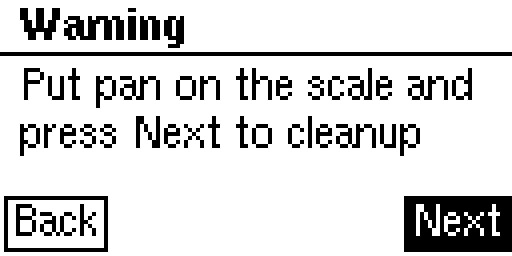
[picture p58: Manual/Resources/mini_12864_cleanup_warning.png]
mini_12864_cleanup_warning


3. You will then see the "Adjust Speed" menu. 

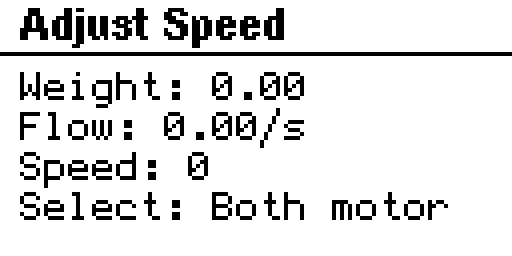
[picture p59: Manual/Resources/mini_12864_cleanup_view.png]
mini_12864_cleanup_view


   At "Adjust Speed" menu, rotate the button clockwise or counter clockwise to adjust the speed of both motors. Use RESET button to exit. Pressing the button downwards will change the control of motors. 

**Validations:**

* If any of, or both motor vibrates, instead of moving clockwise or counter clockwise, you need to swap the middle two pins of the motor cable. 

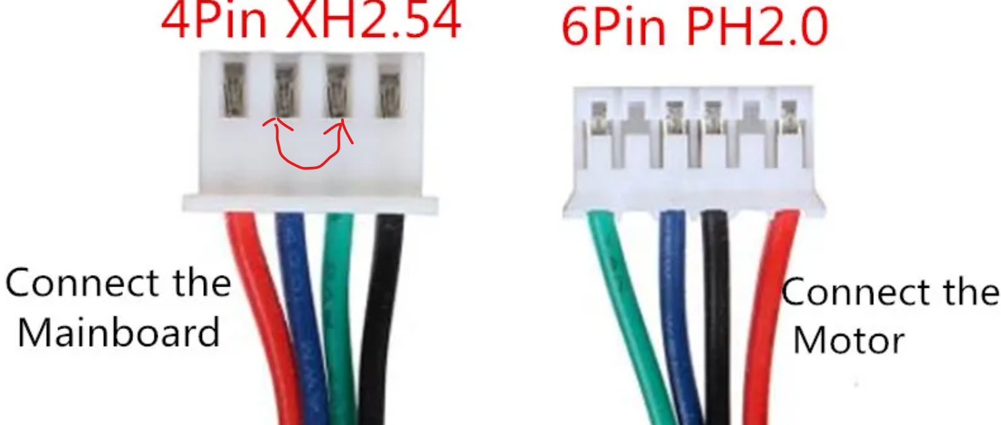
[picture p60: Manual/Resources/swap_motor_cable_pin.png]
swap_motor_cable_pin


* For positive speed, the both motors should rotate clockwise. If not, then you need to invert the motor step direction via the web interface, by toggling "Inverted Step Direction Pin, under "Settings" -> "Coarse Motor", or/and "Fine Motor". You will need to save the settings to the EEPROM and reboot. 

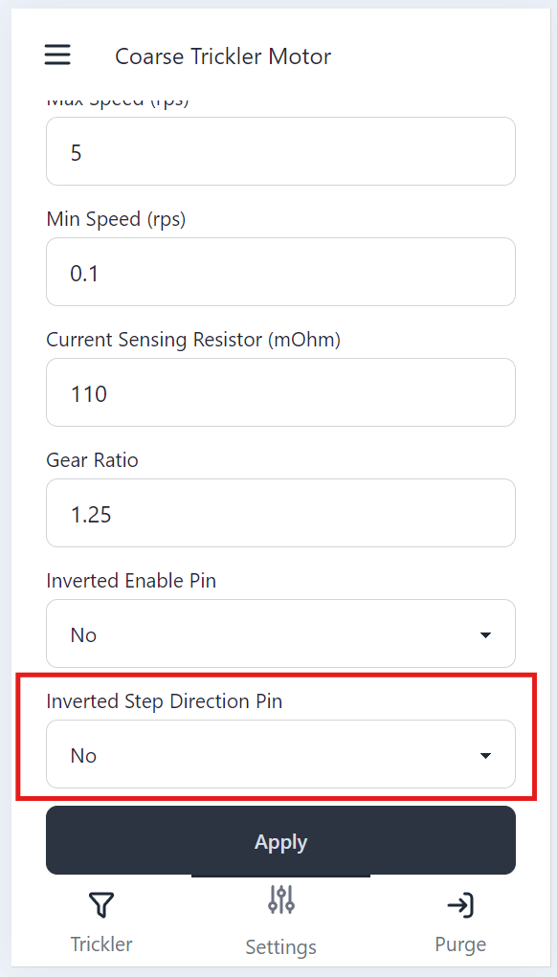
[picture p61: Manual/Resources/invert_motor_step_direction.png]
invert_motor_step_direction


### Configure Fine Trickler Motor Ratio

The OpenTrickler V2 enlarges the outer diameter of the small trickler tube. The number of teeth of the trickler tube also increased. You need to ensure the gear ratio is properly configured. Please use the table below as reference. 

| OpenTrickler Revision | Gear Ratio |
| --- | --- |
| v1.x | 2.105 |
| v2.x | 1.818 |

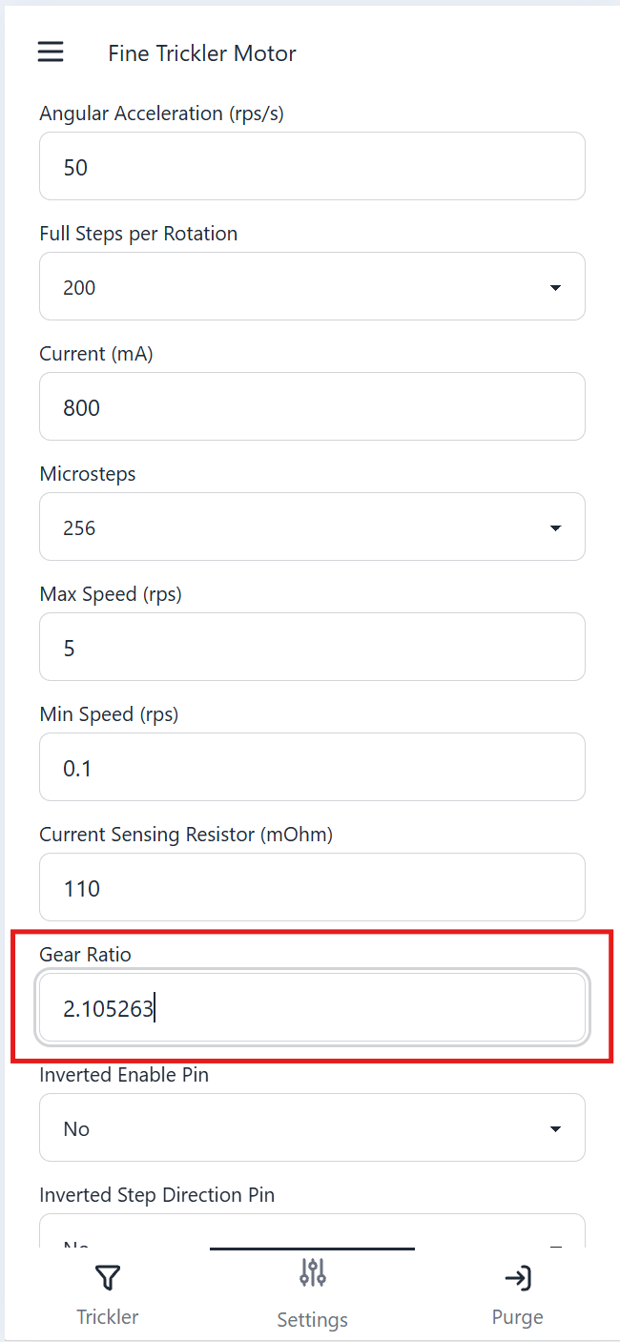
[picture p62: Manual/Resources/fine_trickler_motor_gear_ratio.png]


### Configure and Inspect Scale Communication

* If you're using A&D fx120i/300i series scale, follow the [guide by OE5AMP](https://github.com/eamars/OpenTrickler-RP2040-Controller/blob/main/manuals/OpenTrickler%20manual%20for%20ADFX%20scale.pdf) to configure the scale to report automatically. 
  
  - If your scale was previously configured for AutoTrickler v3/v4, you will only need to follow Step 2 to update the data output mode.

* If you're using G&G J100B scales follow steps from the [guide](https://github.com/eamars/OpenTrickler-RP2040-Controller/blob/main/manuals/configure_g%26g_scales.md).

* If you're using other scales, sorry, at the time this manual is written, the setup procedure for generic scale support is absent. 

Again, the "Cleanup Mode" can be used to validate the scale communication. 

**Steps:**

1. Follow steps from **Inspect Motors** to enter the "Cleanup Mode".
2. Inspect the value after "Weight". 

**Validations"**

* If you read "inf" after the Weight, it indicates the communication to the scale is not established. Please review the connection to the scale, as well as scale settings. 
* If you can read "0" after the Weight, but the value doesn't change despite the value from the scale's screen updated. Please review the scale settings.

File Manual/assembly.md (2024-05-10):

# OpenTrickler Assembly Manual

Depending on the make/model of the scale you're using, you need to follow the print and assembly manual from the following subfolders. 

| Manual\Scale | A&D fx120/300i | G&G JJ100B |
| --- |:---:|:---:|
| [A&D FX Shield](../STL/A&D%20FX%20Shield/README.md) | ✔️ | ❌ |
| [G&G JJ100B housing](../STL/G&G%20JJ100B%20housing/README.md) | ❌ | ✔️ |
| [OpenTrickler](../STL/OpenTrickler/README.md) | ✔️ | ✔️ |
| [Powder Hopper](../STL/Powder%20Hopper/README.md) | ✔️ | ✔️ |

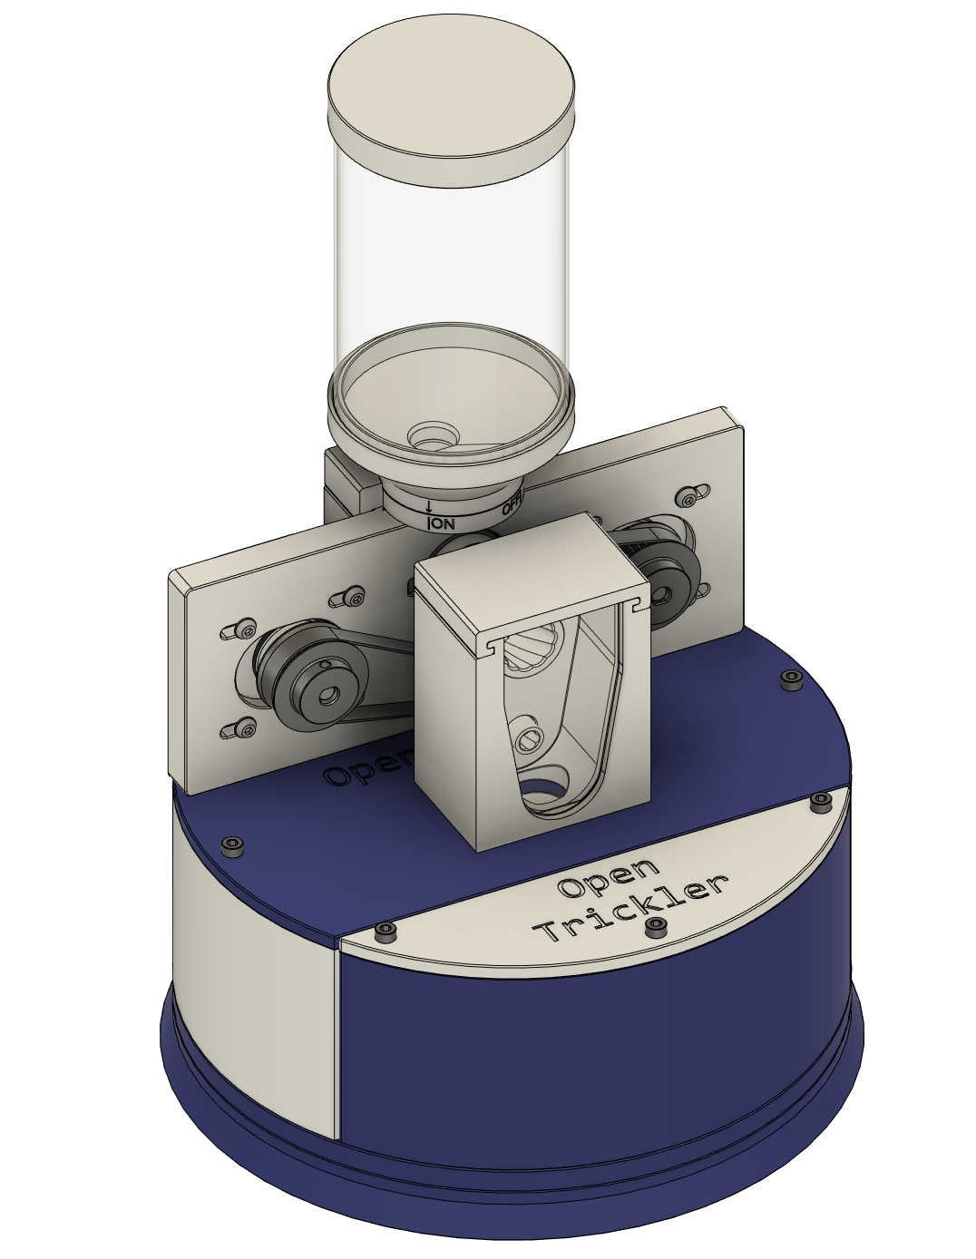
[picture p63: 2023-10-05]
Manual/Resources/fx_shield_final_view.png

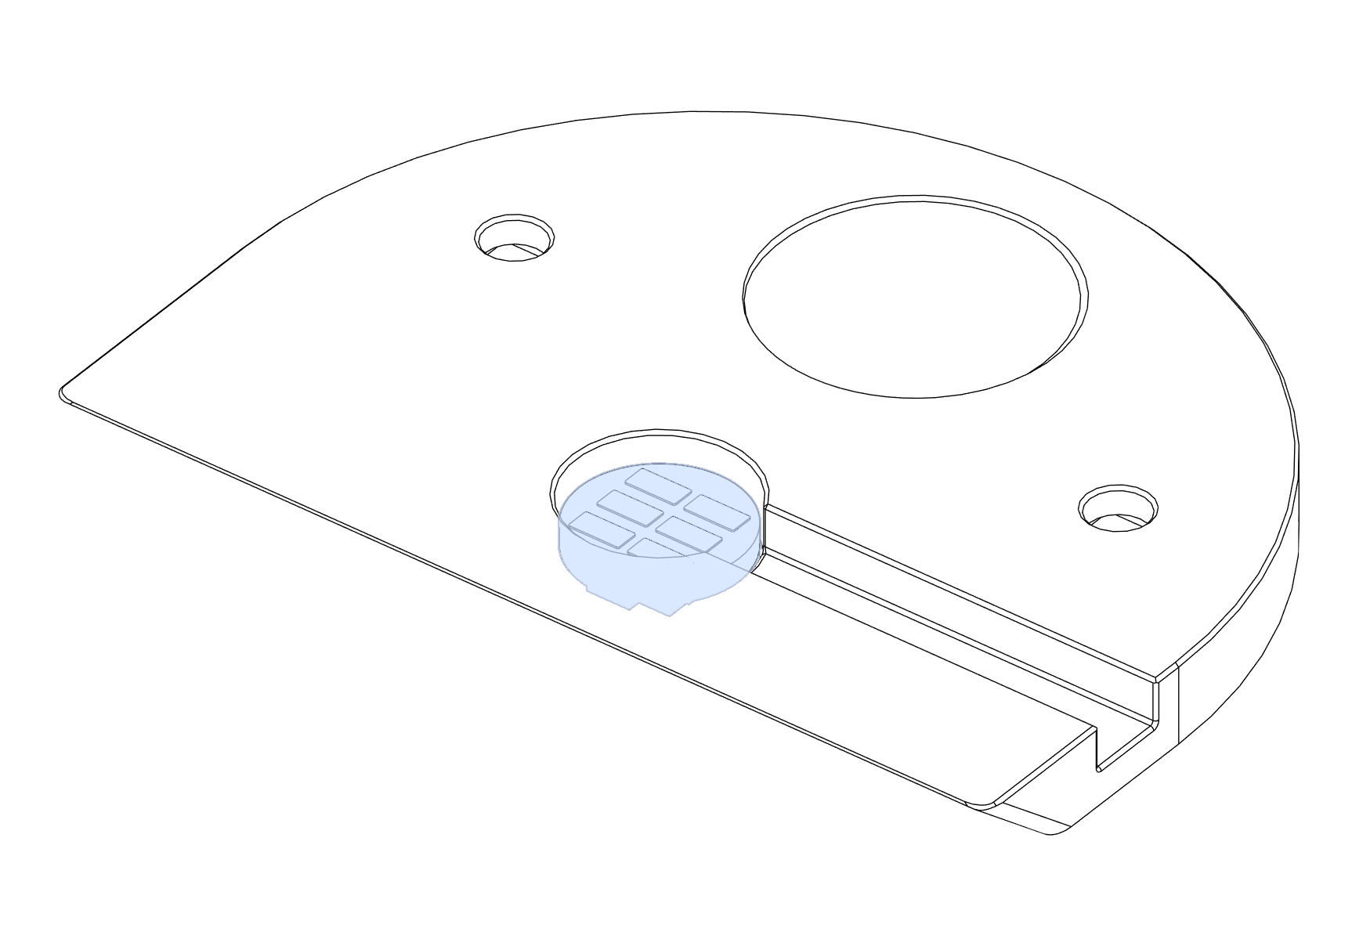
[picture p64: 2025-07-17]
CommunityContributions/eamars/neopixel_led_mod/resources/install_neopixel_at_discharge_port.png

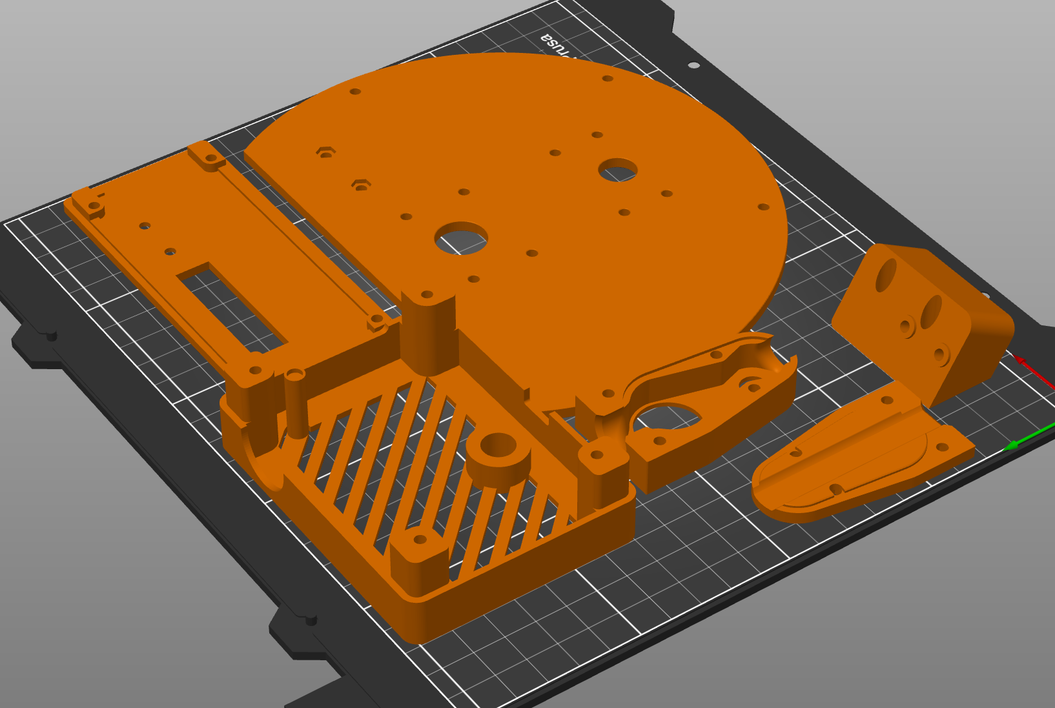
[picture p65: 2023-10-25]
CommunityContributions/dirtbit/print_orientation.png

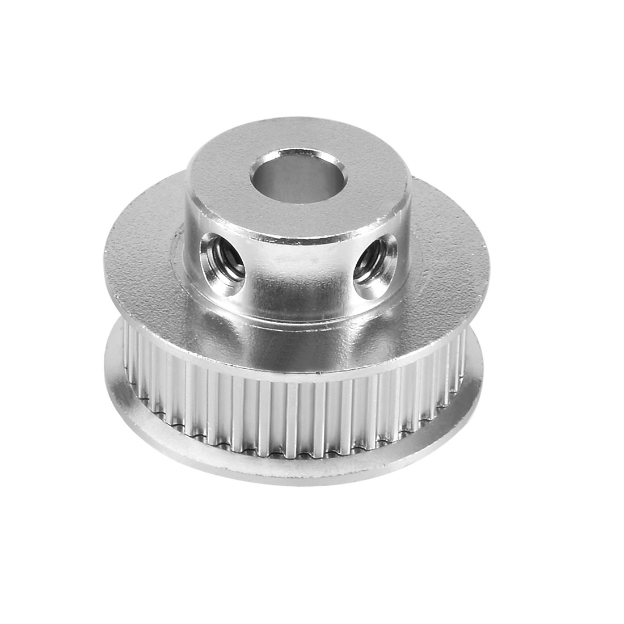
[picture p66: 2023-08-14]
Manual/Resources/gt2_40t_pulley.jpg

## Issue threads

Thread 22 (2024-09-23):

OpenTrickler 2.0 Draft Plan

eamars, 2024-09-23:
Below are OpenTrickler 2.0 proposed changes
* Replace 608 bearing with 6801 (12x22x5) to allow larger fine trickler tubes.
* New coarse and fine trickler tubes.
* Add 0.1mm over travel to servo gates to compensate for print tolerances.
* Fix the print height for each object to ensure the height is the multiple of 0.2mm.
* Fix some design flaws.
* Make the flow reducer and servo gate as default option.

4numen, 2024-09-23:
Reduce flat surface at the bottom of front assembly. Currently causing powder kernels to reside and drop when servo is closing.
Keep front assembly volume as big as possible at the bottom to minimize pre-load covering small tube and kernels jamming.

Issue mostly occurs in front and behind discharge gate.

Possible solution:
-bearing cover with slope below small tube
-front cover also with slope

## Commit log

2021-09-04 Day2 update include stepper motor support as well as the integration of PWM controller vibration motor.
2021-09-06 Date 3 update, fix the mistake in stepper motor driver Implement the PID controller to contol the trickle time for better prevision.
2021-09-14 Add first version of GT2 pully on the powder trickler
    [GT2-60T-635B.SLDPRT, GT2-60T-635B_left.STL, GT2-60T-635B_right.STL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]
2021-09-16 Update pulley assembly design
    [GT2-60T-635B.SLDPRT, GT2-60T-635B_left.STL, GT2-60T-635B_right.STL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]
2021-09-16 Add more mechanical parts
    [Nema17(SY42STH47-1684B)double_shaft.SLDPRT, lee_perfect_powder_measure.SLDPRT, lee_perfect_powder_mounting.SLDPRT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]
2021-10-04 Enlarge the base pad for the scale lid by 1mm
    [scale_lid.SLDPRT, scale_lid.STL, total_assembly.SLDASM]
2021-10-04 Restore the depth of the scale lid to 2.5mm
    [scale_lid.SLDPRT, scale_lid.STL]
2021-10-04 Remove the index pin from the scale lid
    [scale_lid.SLDPRT, scale_lid.STL]
2021-10-04 Update the mounting to minimise the waste material for the mounting base Slice the mounting to exclude the base for printing
    [lee_perfect_powder_mounting.SLDPRT, mounting.SLDPRT, mounting_upper.STL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]
2021-10-07 Update powder measure modling. Add v2 mounting hardware Add drop tube
    [20 Teeth GT2 Pulley.SLDPRT, Nema17(SY42STH47-1684B)double_shaft.SLDPRT, drop_tube.SLDPRT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]
2021-10-07 Update drop tube design
    [drop_tube.SLDPRT, drop_tube.STL]
2021-10-08 Cut some material from the mounting to avoid touching the powder scale
    [lee_perfect_powder_measure_assembly.SLDASM, mounting_v2.SLDPRT, mounting_v2.STL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]
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2021-10-09 optimise v2 drop tube design
    [drop_tube_v2.SLDPRT, drop_tube_v2.STL, mounting_v2.SLDPRT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]
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2021-10-11 Increase the diameter of the bigger pulley Add a prototype of the v2 trickler
    [integrated_trickler.SLDPRT, lee_perfect_powder_measure.SLDPRT, lee_perfect_powder_measure_assembly.SLDASM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]
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2021-10-21 Update v2 integrated trickler design
    [Nema17_pancake.SLDPRT, integrated_trickler_assembly.SLDASM, integrated_trickler_v2.SLDPRT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]
2021-10-25 Some huge update including new designs and the complete PID controller for the new trickler
    [12mm Bearing SKF 6001 RS 334-1528.SLDPRT, 20 Teeth GT2 Pulley.SLDPRT, 20mm Bearing NSK 6804 RS 492-2140.SLDPRT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]
2021-10-26 Update rotary tube design
    [rotary_tube.SLDPRT, rotary_tube.STL]
2021-11-02 Add chassis for electronics
    [4x4_keypad.SLDPRT, duinotech1.3_oled.SLDPRT, electronics_enclosure_assembly.SLDASM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]
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2021-11-06 Update v3 design Update gitignore to ignore solidworks files
    [40_teeth_gt2_pulley.SLDPRT, 40_teeth_gt2_pulley.STL, GT2_50teeth.SLDPRT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]
2021-11-06 Update code to work with v3 trickler
    [integrated_trickler_v3.1_assembly.SLDASM, rotary_tube_v2_big.SLDPRT, rotary_tube_v2_big.STL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]
2021-11-07 Add calibration mode (WIP) Tune the trickler PID controller
    [integrated_trickler_v3.1_assembly.SLDASM, powder_cup.SLDPRT, powder_cup.STL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]
2021-11-09 Replace the 3d printed fine trickling tube with the aluminum one Update the threading for coarse trickling tube Update pid tuning accordingly
    [aluminum_tube_flow_reducer.SLDPRT, aluminum_tube_flow_reducer.STL, aluminum_tube_gear.SLDPRT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]
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2021-11-14 Add 170 and 160mm timing belt design
    [160mm_gt2_timing_belt.SLDPRT, 160mm_gt2_timing_belt.STL, 170mm_gt2_timing_belt.SLDPRT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]
2021-11-17 Update pulley and belt Update large trickling tube Update tuning parameter
    [160mm_gt2_timing_belt.SLDPRT, 160mm_gt2_timing_belt.STL, 170mm_gt2_timing_belt.SLDPRT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]
2021-11-18 improve 40 teeth pulley design
    [40_teeth_gt2_pulley.SLDPRT, 40_teeth_gt2_pulley.STL]
2021-11-21 Minor adjustment to the powder hop connection Update powder cup design to minise the exceesive powder to come out
    [integrated_trickler_v3.1.SLDPRT, integrated_trickler_v3.STL, powder_cup.SLDPRT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]
2021-12-07 Update the flow reducer and front/back panel dimension
    [aluminum_tube_flow_reducer.SLDPRT, aluminum_tube_flow_reducer.STL, front_and_back_panel.SLDPRT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]
2022-03-20 Update the project structure, add 40T GT2 pulley design
    [40T GT2 Pulley.f3d, 40T_GT2_Pulley.stl]
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2022-04-03 Add missing powder channel
    [base_plate_adapter.stl]
2022-04-04 fix the issue where bearing rubs the mounting sourface, fix the compatibility with the existing fx scale lid
    [base_plate_adapter.stl, rear_body.stl]
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2022-04-05 Fix the hole print helper
    [base_plate_adapter.stl]
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2022-04-15 Decrease the inner diameter of the large rotary tube for better printability
    [GT2_82T_Belt.stl, large_rotary_tube.stl]
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2023-03-07 Reorganize the project structure, remove all firmware code
    [12mm Bearing SKF 6001 RS 334-1528.SLDPRT, 160mm_gt2_timing_belt.SLDPRT, 160mm_gt2_timing_belt.STL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]
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2023-05-01 Fix chamfer on rear discharger mount
    [rear_discharge_mount.stl]
2023-05-09 Update tolerance for large rotary tube
    [large_rotary_tube.stl]
2023-05-09 Adjust tolerance
    [large_rotary_tube.stl]
2023-05-10 Implement thicker trickler adapter for more rigid install interface
    [pan_cover_lid.stl, trickler_adapter_plate.stl]
2023-05-12 Tweak few tolerances, add front body cover
    [front_body_cover.stl, lee_bottle_adapter v6.stl, lee_bottle_adapter.stl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]
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2023-05-20 I don't know that is changed, just another export from the CAD to make sure the STL is up-to-date
    [rear_discharge_mount.stl]
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2023-05-21 Update part tolerance, add missing 40T gt2 printable pulley
    [40_teeth_gt2_pulley.STL, rear_discharger_sliding_door.stl]
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2023-08-15 Update sourcing_guide.md
    Fix stepper motor dimension.
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2023-08-16 Fix heatset insert hole diameter
    [hopper_base.stl, powder_hopper_beta1.step, rear_body_interface.stl]
2023-08-16 build in hole tolerance
    [powder_hopper_beta1.step, rear_body_interface.stl]
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2023-08-17 fix orientation
    [rear_body_interface.stl]
2023-08-18 remove tolerance from both side
    [hopper_base.stl, hopper_cap.stl, powder_hopper_beta1.step]
2023-09-16 Fix the orientation of the cap
    [hopper_cap.stl]
2023-09-20 Replace heatset insert with screw thread directly into plastic
    [hopper_base.stl, powder_hopper_beta1.step, powder_hopper_beta2.step]
2023-09-21 Add notch to the hopper interface to lock in place
    [powder_hopper_beta2.step, rear_body_interface.stl]
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2023-09-29 Adjust tolerance of the bearing insert
    [front_body.stl, rear_body.stl]
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2023-10-24 @dirtbit contribution - Display Assy + required Trickler Adapter Plate, Pico Expansion Board enclosure + required OpenTrickler_RearBody, Volume Reduction Inserts for easy cleaning.
    [Display_Assy.step, Display_Assy_body.stl, Display_Assy_bracket.stl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]
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2023-10-25 per @earms request, fixed part orientation and extended instructions / description
    [Display_Assy_body.stl, Display_Assy_bracket.stl, Display_Assy_front.stl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]
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2023-10-28 Fix the exported STL for scale pan cover
    [scale_pan_cover.stl]
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2023-11-25 Add missing fillet
    [trickler_adapter_plate.stl]
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2023-12-24 Update design of front discharger, add alternative tigher tolerance bearing cover
    [[alternative] bearing_cover_tighter_tolerance_x2.stl, front_discharger_mount.stl]
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2024-05-07 fix assembly
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2025-03-14 ian99rt Upload of Pin/Slot Shutter and additional mods
    [Front_Discharge_Plate_+3mm_thicker.3MF, LeftSide_Screen_Bracket_for_dirtBit_Screen_Housing.3mf, LeftandRight_Shutter_Gearless.3mf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]
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2025-07-15 Fix chamfer on both front and rear volume reducer
    [FrontVolumeReductionInsert_Top.stl, RearVolumeReductionInsert_Top.stl]
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2025-07-19 Update missing STL
    [trickler_adapter_plate.stl]
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2025-07-31 small trickler tube and extended servo support mods
    [Extended Servo Support Left.stl, Extended Servo Support Right.stl]
2025-11-23 Update sourcing guide for Raspberry Pi Pico 2W
    Updated references from 'Pico W' to 'Pico 2W' and corrected links. Added note about first gen Pico W support.
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2026-01-28 Add files via upload
    added the shaved front body to test the bearing fit/clearance before doing the full print
    [V2.BodyBearingTest_DeweyMod.stl]
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2026-02-15 Add files via upload
    Reduced and smoothed out intake. Scaled down to 99.7% to help fit inside the bearing.
    [Ultra Low Flow Fine Trickler Tube - Scaled to 99.7 Percent.stl]
